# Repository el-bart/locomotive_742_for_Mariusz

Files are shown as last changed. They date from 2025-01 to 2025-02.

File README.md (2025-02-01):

# locomotive 742

base bodel is from [printables](https://www.printables.com/model/5478-locomotive-742-h0/files).
these are _not_ my files and thus it's not covered by license mentione below.
all my reworks and OpenSCAD models do.

rework to facilitate 5x 0.5V photovoltanic panels, LiPo battery and a DC/DC to keep the LEDs on.
also added some model simplifications for easier FDM 3D printing.

## power budget

while thing is meant to be running from 1S LiPo cell.

5x0.5V at 0.16W PV panels will deliver top current of 64mA.
taking into consideration imperfect lightning conditions, will assume 30mA from now on.
assuming 50% of that time is night, that gives 15mA continuous power that can be used.

DC/DC will typically get 2-2.5V on input.
is to be set to 4.1V on output - i.e. 1S at 90% charge.
taking into consideration low power-output (64mA peak input; half od that output) no additional circuitry
for charge control is needed.

## LEDs

* 4x 5mm red LEDs (rear)
 * 2x 2 LED in sequence, with 2.4k resistor
 * params:
   * 1mA @ 4.1V
   * 0.9mA @ 3.7V
   * LED voltage: 1.78V
* 2x 5mm blue LEDs (interior)
  * 2 LEDs in parallel, sharing 5.6k resistor
  * params:
    * 0.3mA @ 4.1V
    * 0.2mA @ 3.7V
    * LED voltage: 2.5V
* 1x 5mm white LED (front)
  * in sequence with 820 resistor
  * params:
    * 1.9mA @ 4.1V
    * 1.4mA @ 3.7V
    * LED voltage: 2.65V

total current drawage at 4.1V: 4.5mA.

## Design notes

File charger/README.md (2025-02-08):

# USB-C charger

in case model discahrged (e.g. under a snow cap), it can be charged via magnetic port, via USB-C.
it can be connected to a phone or a power bank to get current from.
current is limited to just under 1A.

5V fan is used to cool the transistor.
it's needed if it operates at closed-circuit on output or when high current is needed at low voltage.

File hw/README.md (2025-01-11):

# wiering diagram

## power regulation
DC/DC is not an option, as they tend to shutdown when too much power is requested.
however current from a small PV is, by definition, low.

therefor regular, linear stabilization is used.
LM317 has been selected, with R1=2.2k and R2=5.1k.
this gives `Uout=1.25[V]*(1+R2/R1)~=4.15[V]`.
not that these values may need some adjusting as +-5% resistors will not give exact voltage.
there's also a rectifying diode that will drop by another `0.2[V]`.

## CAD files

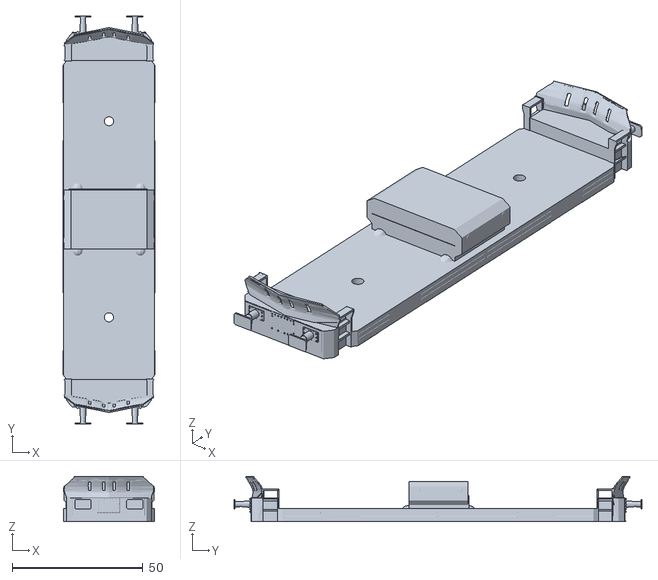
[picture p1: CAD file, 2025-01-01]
model/locomotive_chassis.stl
35.2 x 156.1 x 17.3

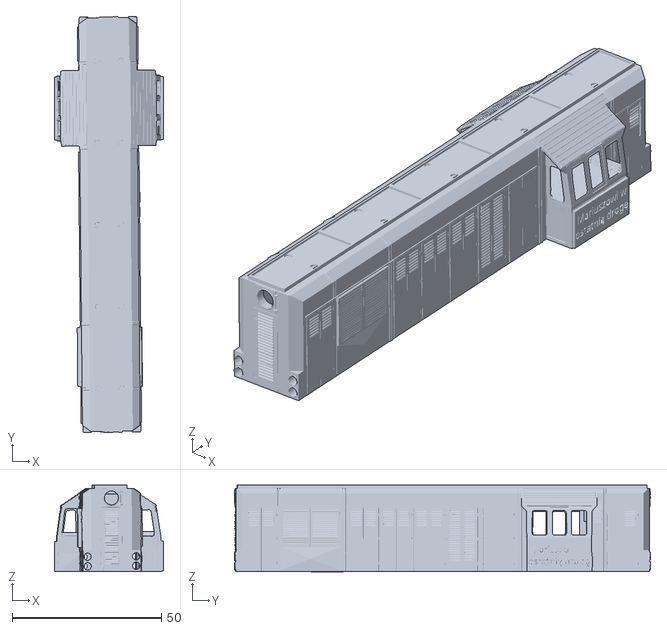
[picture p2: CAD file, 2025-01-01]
model/locomotive_body.stl
36.3 x 139.1 x 29.0

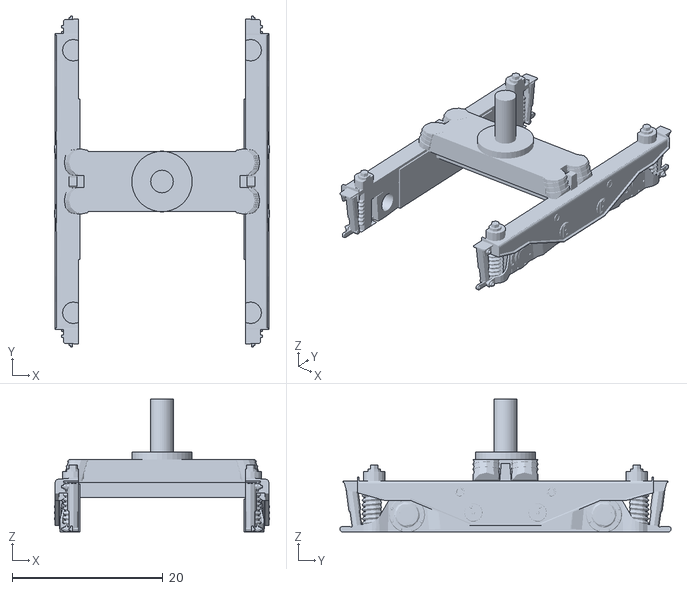
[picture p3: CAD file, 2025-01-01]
model/locomotive_wheel_carriage.stl
28.5 x 43.9 x 17.6

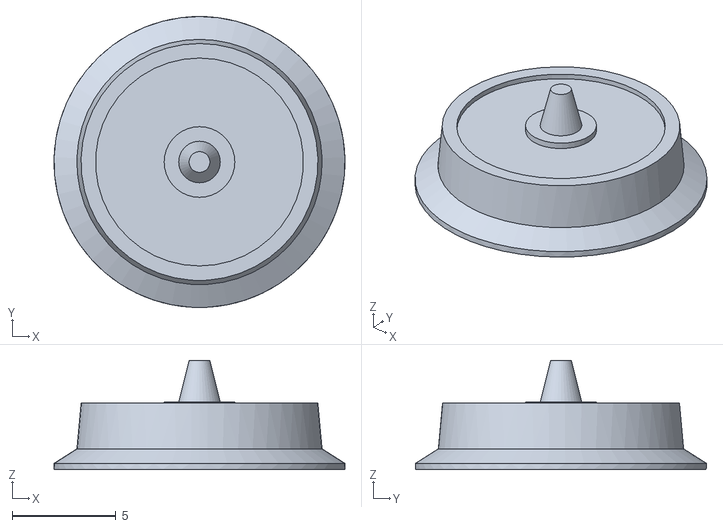
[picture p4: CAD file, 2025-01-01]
model/locomotive_wheel.stl
14.0 x 14.0 x 5.25

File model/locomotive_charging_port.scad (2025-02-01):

include <m3d/all.scad>

magnet_d = 6;
magnet_h = 3;
magnet_surround = 2;
spacing = 0.1;
cable_width = 2.4+0.4;


module magnet_mock()
{
  cylinder(d=magnet_d, h=magnet_h, $fn=fn(20));
}


module charging_port()
{
  w = magnet_surround;
  d = magnet_d;
  side = d+2*w;
  cw = cable_width;
  extra_bottom_h = 1;

  module bottom()
  {
    difference()
    {
      s = side*[1,1,0] + [0,0,magnet_h+extra_bottom_h];
      cube(s);
      translate([s.x/2, s.y/2, -eps])
        cylinder(d=magnet_d+2*spacing, h=magnet_h+2*eps, $fn=fn(50));
    }
  }

  module top()
  {
    translate([0, side, magnet_h+extra_bottom_h])
      rotate([90, 0, 0])
        linear_extrude(side)
          polygon([
            [0, 0],
            [0, d],
            [side, 0]
          ]);
  }

  difference()
  {
    union()
    {
      bottom();
      top();
    }
    // cable hole
    translate([-side/2, side/2-cw/2, magnet_h-eps])
      cube([side, cw, cw+eps]);
  }
}


module charging_plug()
{
  w = magnet_surround;
  s = [magnet_d+2*w, 20, magnet_h+w];
  cw = cable_width;
  rounding = 2;

  difference()
  {
    side_rounded_cube(s, rounding, $fn=fn(20));
    translate([s.x/2, s.y-magnet_d/2-w, 0])
    {
      // magnet slot
      translate([0, 0, w+eps])
      {
        cylinder(d=magnet_d+2*spacing, h=magnet_h+eps, $fn=fn(50));
        %if($preview)
          magnet_mock();
      }
      // bottom cable connection
      translate([0, 0, -eps])
        cylinder(d=cw, h=s.z+2*eps, $fn=fn(50));
      // back cable connection
      translate([-cw/2, -s.y, -eps])
        cube([cw, s.y, cw+eps]);
    }
  }
}


rotate([0, -90, 0])
  charging_port();

translate([3, 0, 0])
  charging_plug();

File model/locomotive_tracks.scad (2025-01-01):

module tracks(length, off)
{
  sleeper_size = [70, 13, 5];
  sleeper_span = 20;

  track_size = [4.3, length, 3];
  track_span = 30.45 + 2*2.3 + 2*0.1;

  module sleeper()
  {
    translate([-sleeper_size.x/2, 0, 0])
      cube(sleeper_size);
  }

  module track(dir)
  {
    dx = dir < 0 ? -track_size.x : 0;
    translate([dx + dir*track_span/2, 0, 0])
      cube(track_size + [0, 0, sleeper_size.z]);
  }

  translate([0, -off, 0])
    for(dir = [-1, +1])
      track(dir);
  for(dy = [0 : sleeper_span+sleeper_size.y : length])
    translate([0, dy, 0])
      sleeper();
}


tracks(length=320, off=5); // ~320mm, with a nice, flat finish at the end

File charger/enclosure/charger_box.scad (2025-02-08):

include <m3d/all.scad>

wall = 0.45*3;

box_size = [45-1.3, 40+5, 40];

fan_size = [40, 40, 10];
fan_spacing = 0.5;
fan_angle = 57; // [deg] from vertical
fan_rim = 1.5;
fan_mount_size = fan_size + (fan_spacing + wall)*[2,2,0] + [0,0,wall];

bottom_space = 10 + wall;

assert(fan_rim > fan_spacing);


module fan_mock()
{
  cube(fan_size);
}

module box()
{
  module main()
  {
    size = box_size;
    difference()
    {
      cube(size);
      translate(wall*[1,1,1])
        cube(size - wall*[2,2,2]);
    }
  }

  module fan_mount()
  {
    size = fan_mount_size;
    module assembly()
    {
      difference()
      {
        cube(size);
        translate(wall*[1,1,0])
        {
          // above-the-rim cut
          translate([0,0,wall])
            cube(fan_size + fan_spacing*[2,2,0] + [0,0,size.z]);
          // in-rim cut
          translate((fan_spacing+fan_rim)*[1,1,0] - [0,0,eps])
          {
            cube(fan_size - fan_rim*[2,2,0] + [0,0,eps]);
          }
          %if($preview)
            translate(fan_spacing*[1,1,0] + [0,0,wall])
              fan_mock();
        }
      }
    }
    translate([0, -size.y, 0])
    assembly();
  }

  module ventilation_holes()
  {
    off = 2;
    cut_size = [30, 3*wall, off];
    for(z=[1:8])
      translate([wall + off, -wall, 8 + z*(off + wall)])
        cube(cut_size);
  }

  module cable_holes()
  {
    translate(wall*[0,-1,1])
    {
      // GND and +5V lines
      dx = wall+2;
      s = [10+2, 5, 5+2];
      for(x=[dx, box_size.x-dx-s.x])
        translate([x, 0, 0])
          cube(s);
      // USB-C socket
      translate([box_size.x-dx-12, box_size.y-wall, 0])
     cube([12, 3*wall, 8]);
    }
  }

  difference()
  {
    main();
    // diagonal cut
    translate([-eps, box_size.y, bottom_space])
      rotate([fan_angle, 0, 0])
        cube(2*[box_size.x, box_size.y, 0] + [0, 0, fan_mount_size.y]);
    ventilation_holes();
    cable_holes();
  }
  // fan_mount assembly
  assert( box_size.x - fan_mount_size.x == 0 );
  translate([-eps, box_size.y, bottom_space])
    rotate([fan_angle-90, 0, 0])
      fan_mount();
}

box();

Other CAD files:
charger/enclosure/m3d/engine/stepper/nema17.scad
charger/enclosure/m3d/all.scad
charger/enclosure/m3d/engine/dc/mt44.scad
charger/enclosure/m3d/engine/dc/mt44_conf.scad
charger/enclosure/m3d/engine/dc/mt83.scad
charger/enclosure/m3d/engine/dc/mt83_conf.scad
charger/enclosure/m3d/fn.scad
charger/enclosure/m3d/inner_shell.scad
charger/enclosure/m3d/map.scad
charger/enclosure/m3d/math.scad
charger/enclosure/m3d/outer_shell.scad
charger/enclosure/m3d/rounded_cube.scad
charger/enclosure/m3d/screw_head_hex.scad
charger/enclosure/m3d/threaded_inserts/cnc_kitchen.scad
model/locomotive_body_pv_top.scad
model/locomotive_plate.scad

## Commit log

2024-12-27 locomotive 742 model
    [742_podvozek_fix4.stl, 742_vrch_meshmixer_fix3.stl, kolonovy.stl]
2024-12-27 3D SDK for locomotive for Mariusz
    [all.scad, cnc_kitchen.scad, fn.scad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]
2024-12-27 draft of models post-processing + configs
    [locomotive_body.scad, locomotive_chassis.scad, locomotive_wheel.scad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]
2024-12-28 a bit simplified chassis model
    [locomotive_chassis.scad, locomotive_chassis.stl]
2024-12-28 body - top removed
    [742_vrch_meshmixer_fix3.stl]
2024-12-28 PV top is now a separate print
    [locomotive_body.scad, locomotive_body_pv_top.scad]
2024-12-28 chassis needs a support material to work
2024-12-28 locomotive is just for preview here
    [locomotive_body_pv_top.scad]
2024-12-28 removed locomotive input - it's replaced by the model with PV panels
    [742_vrch_meshmixer_fix3.stl]
2024-12-28 locomotive_chassis.stl is now a direct STL
    [742_spodek_fix4.stl, locomotive_chassis.stl]
2024-12-28 body (with PV panels) + single wheel as STL directly
    [kolonovy.stl, locomotive_body.stl, locomotive_wheel.scad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]
2024-12-28 locomotive body is now properly leveled on the bed
    [locomotive_body.stl]
2024-12-28 locomotive_wheel_carriage.stl is now a properly positioned STL as well
    [742_podvozek_fix4.stl, locomotive_wheel_carriage.scad, locomotive_wheel_carriage.stl]
2024-12-28 removed lower parts that do not add much but make things difficult to print
    [locomotive_wheel_carriage.stl]
2024-12-28 using common locomotive_body.stl for PV element, too
    [locomotive_body_pv_top.scad]
2024-12-28 locomotive_wheel_carriage with supports
    [locomotive_wheel_carriage.stl]
2024-12-28 simplified locomitive chassis
    [locomotive_chassis.stl]
2024-12-28 removed logo
    [locomotive_chassis.stl]
2024-12-28 body update - removed all unwelcomed elements
    [locomotive_body.stl]
2024-12-28 turned ut that carriage does nto need support after all
2024-12-28 plate with the message
    [locomotive_plate.scad]
2024-12-28 font decreased a bit
    [locomotive_plate.scad]
2024-12-28 model with side plates merged in
    [locomotive_body.stl]
2024-12-28 managed to fix model, so that no empty layers show up
    [locomotive_body.stl]
2024-12-29 put down power budget info
2024-12-29 LEDs setup and measurements
2024-12-31 tracks to put locomotive on
    [locomotive_tracks.scad]
2025-01-01 dimensions adjusted - apparent whole thing is not a scale factor...
    [locomotive_tracks.scad]
2025-01-01 reworked tracks - using values that look approximately ok, intead of scaling factors, that does not seem to play well with the actual model
    [locomotive_tracks.scad]
2025-01-01 moved everything out from the top directory
    [all.scad, cnc_kitchen.scad, fn.scad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]
2025-01-01 Revert "moved everything out from the top directory"
    This reverts commit 9377f5a7aff41bbca460a25ef3f31e737107e3e1.
    [all.scad, cnc_kitchen.scad, fn.scad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]
2025-01-01 model dir renamed
    [all.scad, cnc_kitchen.scad, fn.scad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]
2025-01-01 added note about license of the original files + LiPo cell
2025-01-01 tracks adjusted, so that they fit on the bed nicely
    [locomotive_tracks.scad]
2025-01-11 KiCad SDK
2025-01-11 empty KiCad project
    [locomotive_electronics.kicad_pcb, locomotive_electronics.kicad_sch]
2025-01-11 schematics of electronics
    [locomotive_electronics.kicad_sch]
2025-01-11 description of wiring diagram
2025-02-01 3D SDK bump
    [all.scad]
2025-02-01 placeholder for charging element(s)
    [locomotive_charging_port.scad]
2025-02-01 charging_plug module
    [locomotive_charging_port.scad]
2025-02-01 charging port elements are 1.0 scale and 100% infill
2025-02-01 addded magnet mock to the picture
    [locomotive_charging_port.scad]
2025-02-01 charnging port added
    [locomotive_charging_port.scad]
2025-02-01 2x charging port for +/- sides
2025-02-01 power calc fixed for better display on GH
2025-02-01 adjusted cable slot for a better fit
    [locomotive_charging_port.scad]
2025-02-08 description of the charger block
2025-02-08 3D SDK for charger enclosure
    [all.scad, cnc_kitchen.scad, fn.scad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]
2025-02-08 printing in ASA
2025-02-08 fan mount draft + box draft
    [charger_box.scad]
2025-02-08 main shape, w/o ventilation / cable holes
    [charger_box.scad]
2025-02-08 box with larger cable holes
    [charger_box.scad]
2025-02-08 KiCad SDK for charger
2025-02-08 empty charger schematic
    [charger.kicad_pcb, charger.kicad_sch]
2025-02-08 added schematics of the charger
    [charger.kicad_sch]
